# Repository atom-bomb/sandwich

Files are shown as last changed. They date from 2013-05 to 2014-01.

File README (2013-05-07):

Sandwich is a project to create low-cost electronics for 3D printing and CNC using an ATMEGA644p and TB6600 stepper drivers, not entirely unlike http://www.reprap.org/wiki/Gen7T and http://www.reprap.org/wiki/Sanguish.

The goal is to make an easily built, free and open design capable of running the Marlin firmware that can be built for around $40.

Design work is currently being done in the hobbyist-friendly Eagle CAD.
If the design exceeds the limits of the free version of Eagle CAD, the design will likely be ported to gEDA or another free CAD system in order to support the free and open design goal.

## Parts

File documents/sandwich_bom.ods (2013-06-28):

Qty | Value | Device | Package | Parts | Description | Tayda Part Number | Tayda Price / ea | Tayda Subtotal | Mouser Part Number | Mouser Price / ea | Mouser Subtotal
4 |  | JP4Q | JP4Q | JP0, JP1, JP2, JP3 | JUMPER | A-198 (http://www.taydaelectronics.com/connectors-sockets/pin-headers/2x40-pin-2-54-mm-double-row-pin-header-strip.html) | 0.28
2 |  | LED5MM | LED5MM | LED1, LED2 | LED | A-1554 (http://www.taydaelectronics.com/leds/round-leds/5mm-leds/led-5mm-red.html) | 0.02 | 0.04
3 |  | M02PTH3 | 1X02_LONGPADS | FAN, TEMP0, TEMP1 | Header 2 | A-197 (http://www.taydaelectronics.com/connectors-sockets/pin-headers/40-pin-2-54-mm-single-row-pin-header-strip.html) | 0.15
3 |  | M03LONGPADS | 1X03_LONGPADS | X_MIN, Y_MIN, Z_MIN | Header 3
1 |  | M06SIP | 1X06 | SER0 | Header 6
19 | 0.1uF | CAPPTH | CAP-PTH-SMALL | C5, C6, C7, C9, C11, C14, C15, C16, C19, C20, C21, C24, C25, C26, C27, C28, C29, C30, C31 | Capacitor | A-553 (http://www.taydaelectronics.com/capacitors/ceramic-disc-capacitors/10-x-0-1uf-50v-ceramic-disc-capacitor-pkg-of-27.html) | 0.01 | 0.19
32 | 1 | R-US_0204/2V | 0204V | R2, R3, R4, R5, R6, R7, R8, R9, R20, R21, R22, R23, R24, R25, R26, R27, R32, R33, R34, R35, R36, R37, R38, R39, R44, R45, R46, R47, R48, R49, R50, R51 | RESISTOR, American symbol | A-2031 (http://www.taydaelectronics.com/resistors/1-4w-carbon-film-resistors/10-x-resistor-1-ohm-1-4w-5-carbon-film-pkg-of-10.html) | 0.01 | 0.32
8 | 100uF | CAP_POLPTH2 | CPOL-RADIAL-10UF-25V | C3, C4, C12, C13, C17, C18, C22, C23 | Capacitor Polarized | A-4514 (http://www.taydaelectronics.com/capacitors/electrolytic-capacitors/100uf-16v-105c-radial-electrolytic-capacitor-5x11mm.html) | 0.02 | 0.16
1 | 10k | R-US_0204/2V | 0204V | R1 | RESISTOR, American symbol | A-2115 (http://www.taydaelectronics.com/resistors/1-4w-carbon-film-resistors/10-x-resistor-10k-ohm-1-4w-5-carbon-film-pkg-of-10.html) | 0.01 | 0.01
2 | 10uF | CAP_POLPTH2 | CPOL-RADIAL-10UF-25V | C8, C10 | Capacitor Polarized | A-4534 (http://www.taydaelectronics.com/capacitors/electrolytic-capacitors/10uf-25v-105c-radial-electrolytic-capacitor-5x11mm.html) | 0.02 | 0.04
2 | 1N4004 | 1N4004 | DO41-10 | D1, D2 | DIODE | A-156 (http://www.taydaelectronics.com/diodes/standard/1n4004-diode-1a-400v.html) | 0.02 | 0.04
1 | 1N4004 | DIODEPTH | DIODE-1N4001 | D3 | Diode
10 | 1k | R-US_0204/2V | 0204V | R12, R13, R14, R17, R30, R31, R42, R43, R54, R55 | RESISTOR, American symbol | A-2123 (http://www.taydaelectronics.com/resistors/1-4w-carbon-film-resistors/10-x-resistor-1k-ohm-1-4w-5-carbon-film-pkg-of-10.html) | 0.01 | 0.1
1 | 1k7 | R-US_0204/2V | 0204V | R56 | RESISTOR, American symbol | A-2084 (http://www.taydaelectronics.com/resistors/1-4w-carbon-film-resistors/10-x-resistor-1-6k-ohm-1-4w-5-carbon-film-pkg-of-10.html) | 0.01 | 0.01
1 | 20MHZ | XTAL/S | QS | Q1 | CRYSTAL | A-236 (http://www.taydaelectronics.com/crystals-resonators-oscilliators/crystals/20-000-mhz-20-mhz-crystal-hc-49-s-low-profile.html) | 0.1 | 0.1
2 | 22pF | CAPPTH2 | CAP-PTH-SMALL2 | C1, C2 | Capacitor | A-523 (http://www.taydaelectronics.com/capacitors/ceramic-disc-capacitors/10-x-22pf-50v-ceramic-disc-capacitor-pkg-of-10.html) | 0.01 | 0.02
1 | 2N2222 | 2N2222 | TO18 | T4 | NPN TRANSISTOR | A-113 (http://www.taydaelectronics.com/t-transistors/2n-series/2n2222a-2n2222-npn-transistor-0-8a-40v-to-18.html) | 0.33 | 0.33
4 | 4.7k | POTTRIM | TRIM_POT | T0, T1, T2, T3 |  | A-2511 (http://www.taydaelectronics.com/potentiometer-variable-resistors/trimmers/6mm-top-adjustment/4-7k-ohm-trimpot-variable-resistor-6mm.html) | 0.06 | 0.24
4 | 4.7k | R-US_0204/2V | 0204V | R11, R29, R41, R53 | RESISTOR, American symbol | A-2027 (http://www.taydaelectronics.com/resistors/1-4w-carbon-film-resistors/10-x-resistor-4-7k-4k7-ohm-1-4w-5-carbon-film-pkg-of-10.html) | 0.01 | 0.04
4 | 47k | R-US_0204/2V | 0204V | R10, R28, R40, R52 | RESISTOR, American symbol | A-2066 (http://www.taydaelectronics.com/resistors/1-4w-carbon-film-resistors/10-x-resistor-47k-ohm-1-4w-5-carbon-film-pkg-of-10.html) | 0.01 | 0.04
2 | 4k7 | R-US_0204/2V | 0204V | R16, R19 | RESISTOR, American symbol | A-2027 (http://www.taydaelectronics.com/resistors/1-4w-carbon-film-resistors/10-x-resistor-4-7k-4k7-ohm-1-4w-5-carbon-film-pkg-of-10.html) | 0.01 | 0.02
2 | 560 | R-US_0204/2V | 0204V | R15, R18 | RESISTOR, American symbol | A-2065 (http://www.taydaelectronics.com/resistors/1-4w-carbon-film-resistors/10-x-resistor-560-ohm-1-4w-5-carbon-film-pkg-of-10.html) | 0.01 | 0.02
1 | ATMEGA644-20PU | ATMEGA644-20PU | DIL40 | IC1 | 8-bit Microcontroller with 64K Bytes In-System Programmable Flash |  |  |  | 556-ATMEGA644PA-PU (http://www.mouser.com/ProductDetail/Atmel/ATmega644PA-PU/?qs=sGAEpiMZZMutXGli8Ay4kJfLPaXdJsZCnXM01wXS9Ts=) | 7.5 | 7.5
1 | AVR_SPI_PRG_6NS | AVR_SPI_PRG_6NS | 2X3-NS | J1 | AVR ISP 6 Pin
3 | DG3XX-02-3.5 | DG3XX-02-3.5 | DG350-3.5-02P | HEATER0, HEATER1, V+ | DG350-3.5-02P | A-4569 (http://www.taydaelectronics.com/connectors-sockets/terminal-blocks/pcb-mount/dg350-screw-terminal-block-2-positions-3-5mm.html) | 0.15 | 0.45
4 | DG3XX-04-3.5 | DG3XX-04-3.5 | DG350-3.5-04P | MOTOR0, MOTOR1, MOTOR2, MOTOR3 | DG350-3.5-04P
2 | MOSFET-NCHANNELFQP30N06L | MOSFET-NCHANNELFQP30N06L | TO220V | Q2, Q3 | Common NMOSFET Parts | A-082 (http://www.taydaelectronics.com/t-transistors/fets-mosfets/irfz44-irfz44n-mosfet-n-channel-49a-55v.html) | 0.45 | 0.9
4 | TB6600HG | TB6600HG | P-HZIP25-1.00G | U$1, U$2, U$3, U$4 |  |  |  |  | 757-TB6600HGO (http://www.mouser.com/ProductDetail/Toshiba/TB6600HGO/?qs=/ha2pyFaduir2PxFYWpWDfA69NCKMQC2ZOZZFkxtsnE=) | 7.5 | 30
 |  |  |  |  |  |  |  | 3.07 |  |  | 37.5

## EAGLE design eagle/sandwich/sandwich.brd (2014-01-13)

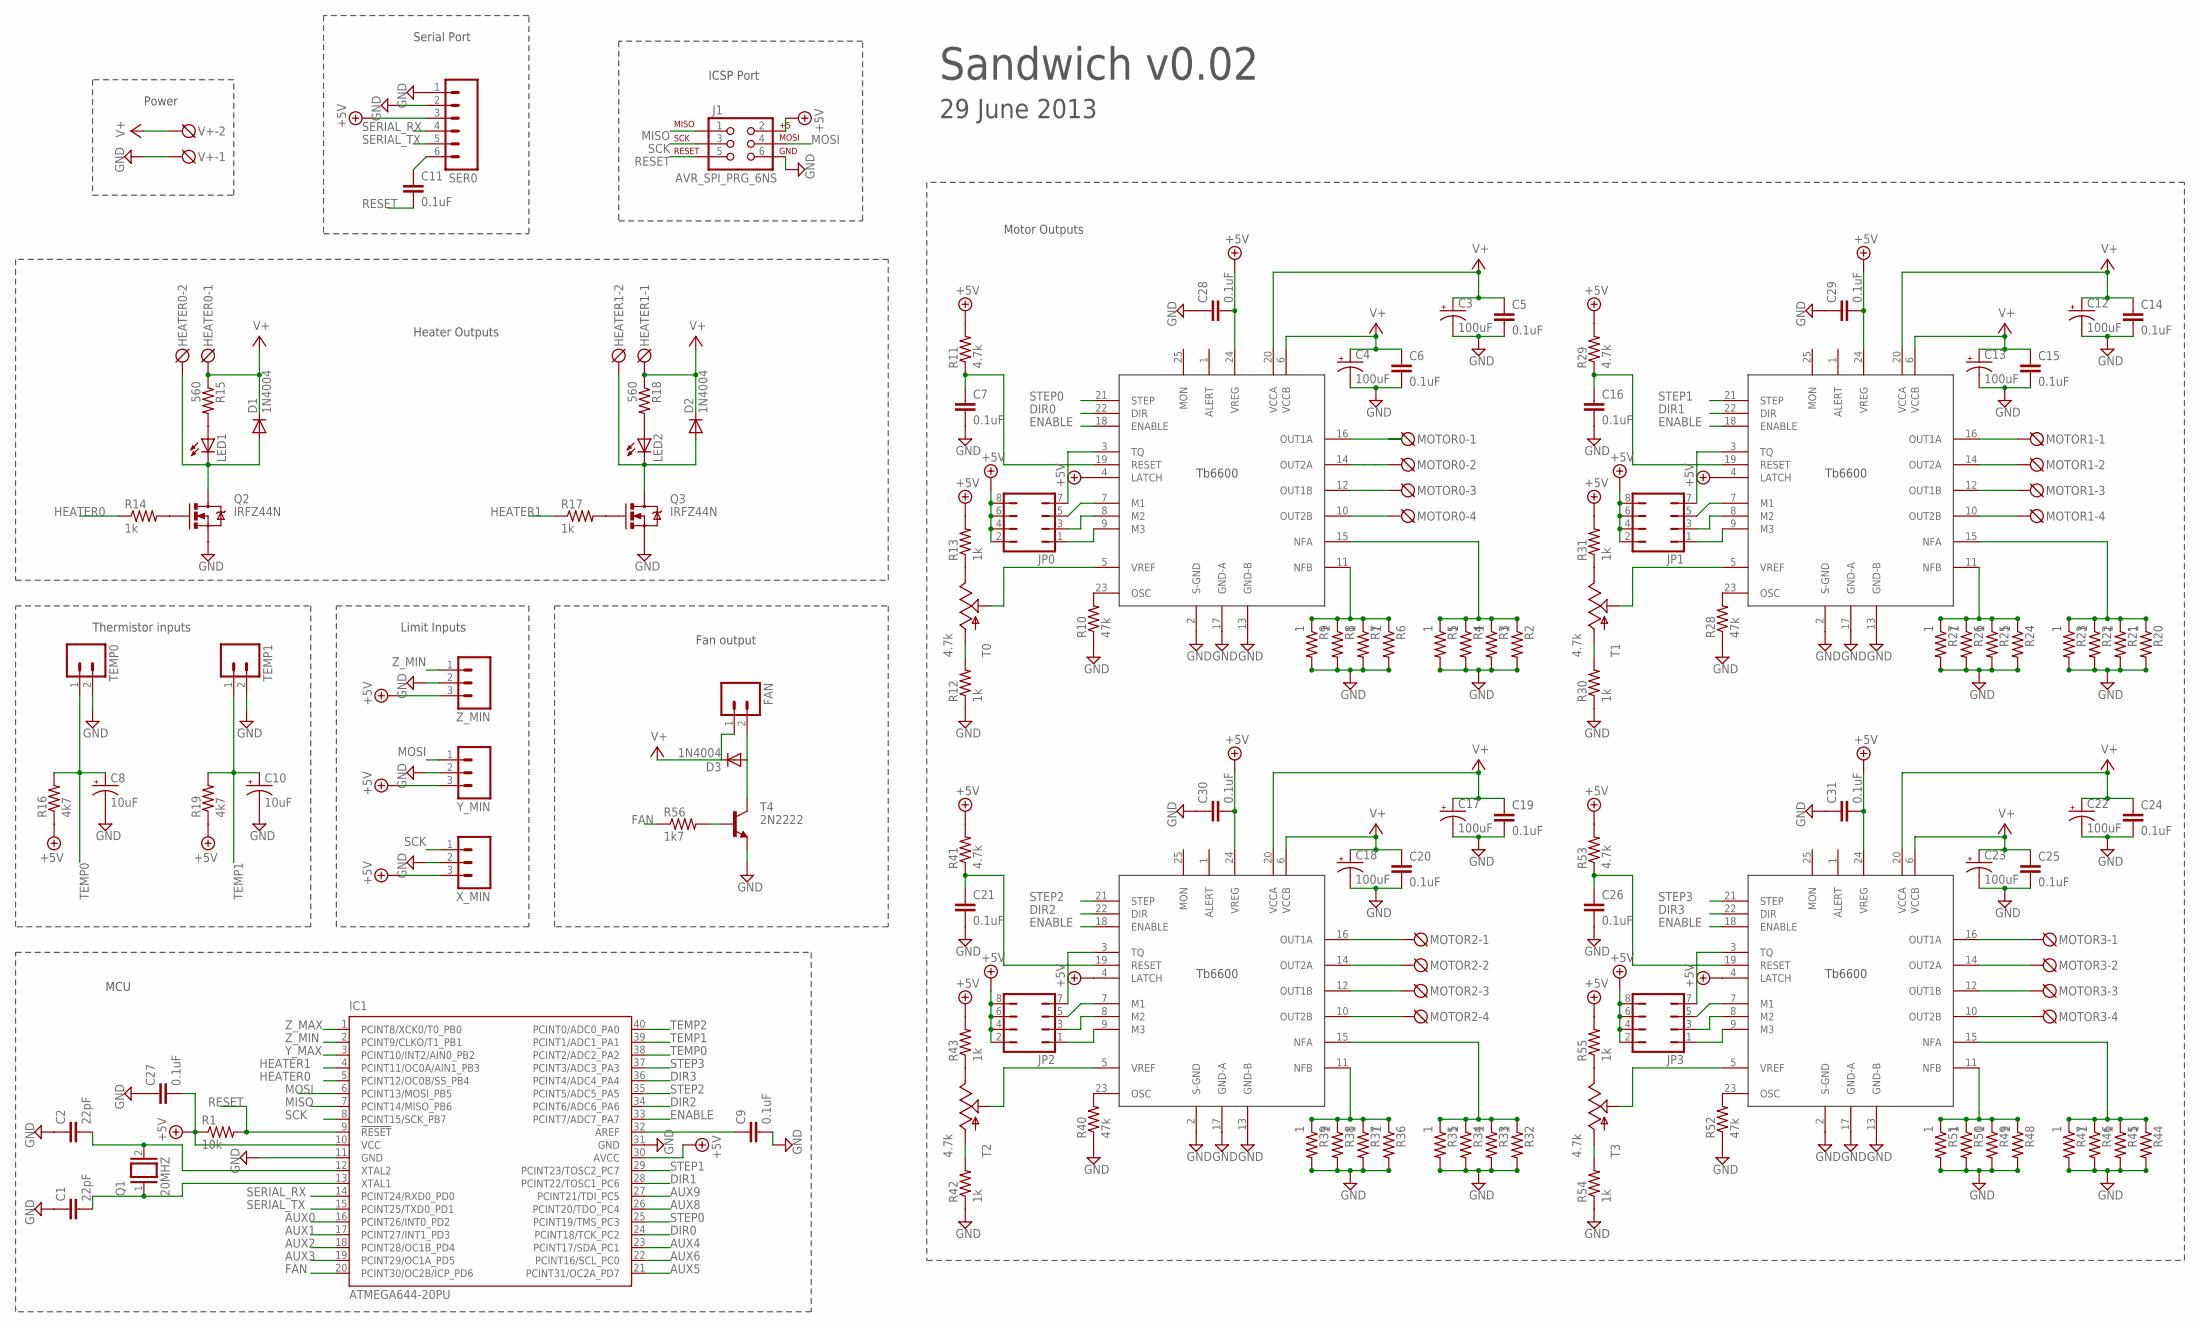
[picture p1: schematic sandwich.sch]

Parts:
C1, C2: 22pF; CAP-PTH-SMALL2
C3, C4, C12, C13, C17, C18, C22, C23: 100uF; CPOL-RADIAL-10UF-25V
C5, C6, C7, C9, C11, C14, C15, C16, C19, C20, C21, C24, C25, C26, C27, C28, C29, C30, C31: 0.1uF; CAP-PTH-SMALL
C8, C10: 10uF; CPOL-RADIAL-10UF-25V
D1, D2: 1N4004; DO41-10
D3: 1N4004; DIODE-1N4001
FAN: M02PTH3; 1X02_LONGPADS
HEATER0, HEATER1: DG3XX-02-3.5; DG350-3.5-02P
IC1: ATMEGA644-20PU; DIL40
J1: AVR_SPI_PRG_6NS; 2X3-NS
JP0, JP1, JP2, JP3: JP4Q
LED1, LED2: LED5MM
MOTOR0, MOTOR1, MOTOR2, MOTOR3: DG3XX-04-3.5; DG350-3.5-04P
Q1: 20MHZ; QS
Q2, Q3: IRFZ44N; TO220V
R1: 10k; 0204V
R2, R3, R4, R5, R6, R7, R8, R9, R20, R21, R22, R23, R24, R25, R26, R27, R32, R33, R34, R35, R36, R37, R38, R39, R44, R45, R46, R47, R48, R49, R50, R51: 1; 0204V
R10, R28, R40, R52: 47k; 0204V
R11, R29, R41, R53: 4.7k; 0204V
R12, R13, R14, R17, R30, R31, R42, R43, R54, R55: 1k; 0204V
R15, R18: 560; 0204V
R16, R19: 4k7; 0204V
R56: 1k7; 0204V
SER0: M06SIP; 1X06
T0, T1, T2, T3: 4.7k; TRIM_POT
T4: 2N2222; TO18
TEMP0, TEMP1: M02PTH3; 1X02_LONGPADS
U$1, U$2, U$3, U$4: TB6600HG; P-HZIP25-1.00G
V+: DG3XX-02-3.5; DG350-3.5-02P
X_MIN: M03LONGPADS; 1X03_LONGPADS
Y_MIN: M03LONGPADS; 1X03_LONGPADS
Z_MIN: M03LONGPADS; 1X03_LONGPADS

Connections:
+5V: C27.2, C28.2, C29.2, C30.2, C31.2, IC1.10 (VCC), IC1.30 (AVCC), J1.2, JP0.2, JP0.4, JP0.6, JP0.8, JP1.2, JP1.4, JP1.6, JP1.8, JP2.2, JP2.4, JP2.6, JP2.8, JP3.2, JP3.4, JP3.6, JP3.8, R1.1, R11.2, R13.2, R16.1, R19.1, R29.2, R31.2, R41.2, R43.2, R53.2, R55.2, SER0.3, U$1.4 (LATCH), U$1.24 (VREG), U$2.4 (LATCH), U$2.24 (VREG), U$3.4 (LATCH), U$3.24 (VREG), U$4.4 (LATCH), U$4.24 (VREG), X_MIN.3, Y_MIN.3, Z_MIN.3
AUX0: IC1.16 (PCINT26/INT0_PD2)
AUX1: IC1.17 (PCINT27/INT1_PD3)
AUX2: IC1.18 (PCINT28/OC1B_PD4)
AUX3: IC1.19 (PCINT29/OC1A_PD5)
AUX4: IC1.23 (PCINT17/SDA_PC1)
AUX5: IC1.21 (PCINT31/OC2A_PD7)
AUX6: IC1.22 (PCINT16/SCL_PC0)
AUX8: IC1.26 (PCINT20/TDO_PC4)
AUX9: IC1.27 (PCINT21/TDI_PC5)
DIR0: IC1.24 (PCINT18/TCK_PC2), U$1.22 (DIR)
DIR1: IC1.28 (PCINT22/TOSC1_PC6), U$2.22 (DIR)
DIR2: IC1.34 (PCINT6/ADC6_PA6), U$3.22 (DIR)
DIR3: IC1.36 (PCINT4/ADC4_PA4), U$4.22 (DIR)
ENABLE: IC1.33 (PCINT7/ADC7_PA7), U$1.18 (ENABLE), U$2.18 (ENABLE), U$3.18 (ENABLE), U$4.18 (ENABLE)
FAN: IC1.20 (PCINT30/OC2B/ICP_PD6), R56.1
GND: C1.1, C2.1, C3.2 (-), C4.2 (-), C5.2, C6.2, C7.2, C8.2 (-), C9.2, C10.2 (-), C12.2 (-), C13.2 (-), C14.2, C15.2, C16.2, C17.2 (-), C18.2 (-), C19.2, C20.2, C21.2, C22.2 (-), C23.2 (-), C24.2, C25.2, C26.2, C27.1, C28.1, C29.1, C30.1, C31.1, IC1.11 (GND), IC1.31 (GND), J1.6, Q2.3 (S), Q3.3 (S), R2.2, R3.2, R4.2, R5.2, R6.2, R7.2, R8.2, R9.2, R10.1, R12.1, R20.2, R21.2, R22.2, R23.2, R24.2, R25.2, R26.2, R27.2, R28.1, R30.1, R32.2, R33.2, R34.2, R35.2, R36.2, R37.2, R38.2, R39.2, R40.1, R42.1, R44.2, R45.2, R46.2, R47.2, R48.2, R49.2, R50.2, R51.2, R52.1, R54.1, SER0.1, SER0.2, T4.1 (E), TEMP0.2, TEMP1.2, U$1.2 (S-GND), U$1.13 (GND-B), U$1.17 (GND-A), U$2.2 (S-GND), U$2.13 (GND-B), U$2.17 (GND-A), U$3.2 (S-GND), U$3.13 (GND-B), U$3.17 (GND-A), U$4.2 (S-GND), U$4.13 (GND-B), U$4.17 (GND-A), V+.1, X_MIN.2, Y_MIN.2, Z_MIN.2
HEATER0: IC1.5 (PCINT12/OC0B/SS_PB4), R14.1
HEATER1: IC1.4 (PCINT11/OC0A/AIN1_PB3), R17.1
MISO: IC1.7 (PCINT14/MISO_PB6), J1.1
MOSI: IC1.6 (PCINT13/MOSI_PB5), J1.4, Y_MIN.1
unnamed: C2.2, IC1.12 (XTAL2), Q1.2
unnamed: C1.2, IC1.13 (XTAL1), Q1.1
unnamed: R10.2, U$1.23 (OSC)
unnamed: R2.1, R3.1, R4.1, R5.1, U$1.15 (NFA)
unnamed: R6.1, R7.1, R8.1, R9.1, U$1.11 (NFB)
unnamed: MOTOR0.4, U$1.10 (OUT2B)
unnamed: MOTOR0.3, U$1.12 (OUT1B)
unnamed: MOTOR0.2, U$1.14 (OUT2A)
unnamed: MOTOR0.1, U$1.16 (OUT1A)
unnamed: R12.2, T0.3 (A)
unnamed: R13.1, T0.2 (E)
unnamed: T0.1 (S), U$1.5 (VREF)
unnamed: Q2.1 (G), R14.2
unnamed: LED1.A, R15.2
unnamed: D1.A, HEATER0.2, LED1.K (C), Q2.2 (D)
unnamed: C7.1, R11.1, U$1.19 (RESET)
unnamed: C9.1, IC1.32 (AREF)
unnamed: JP0.1, U$1.9 (M3)
unnamed: Q3.1 (G), R17.2
unnamed: LED2.A, R18.2
unnamed: D2.A, HEATER1.2, LED2.K (C), Q3.2 (D)
unnamed: JP0.3, U$1.8 (M2)
unnamed: JP0.5, U$1.7 (M1)
unnamed: JP0.7, U$1.3 (TQ)
unnamed: C11.1, SER0.6
unnamed: D3.A, FAN.2, T4.3 (C)
unnamed: R20.1, R21.1, R22.1, R23.1, U$2.15 (NFA)
unnamed: R24.1, R25.1, R26.1, R27.1, U$2.11 (NFB)
unnamed: R28.2, U$2.23 (OSC)
unnamed: MOTOR1.1, U$2.16 (OUT1A)
unnamed: MOTOR1.2, U$2.14 (OUT2A)
unnamed: MOTOR1.3, U$2.12 (OUT1B)
unnamed: MOTOR1.4, U$2.10 (OUT2B)
unnamed: C16.1, R29.1, U$2.19 (RESET)
unnamed: R30.2, T1.3 (A)
unnamed: R31.1, T1.2 (E)
unnamed: T1.1 (S), U$2.5 (VREF)
unnamed: JP1.1, U$2.9 (M3)
unnamed: JP1.3, U$2.8 (M2)
unnamed: JP1.5, U$2.7 (M1)
unnamed: JP1.7, U$2.3 (TQ)
unnamed: R32.1, R33.1, R34.1, R35.1, U$3.15 (NFA)
unnamed: R36.1, R37.1, R38.1, R39.1, U$3.11 (NFB)
unnamed: R40.2, U$3.23 (OSC)
unnamed: MOTOR2.1, U$3.16 (OUT1A)
unnamed: MOTOR2.2, U$3.14 (OUT2A)
unnamed: MOTOR2.3, U$3.12 (OUT1B)
unnamed: MOTOR2.4, U$3.10 (OUT2B)
unnamed: C21.1, R41.1, U$3.19 (RESET)
unnamed: R42.2, T2.3 (A)
unnamed: R43.1, T2.2 (E)
unnamed: T2.1 (S), U$3.5 (VREF)
unnamed: JP2.1, U$3.9 (M3)
unnamed: JP2.3, U$3.8 (M2)
unnamed: JP2.5, U$3.7 (M1)
unnamed: JP2.7, U$3.3 (TQ)
unnamed: R44.1, R45.1, R46.1, R47.1, U$4.15 (NFA)
unnamed: R48.1, R49.1, R50.1, R51.1, U$4.11 (NFB)
unnamed: R52.2, U$4.23 (OSC)
unnamed: MOTOR3.1, U$4.16 (OUT1A)
unnamed: MOTOR3.2, U$4.14 (OUT2A)
unnamed: MOTOR3.3, U$4.12 (OUT1B)
unnamed: MOTOR3.4, U$4.10 (OUT2B)
unnamed: C26.1, R53.1, U$4.19 (RESET)
unnamed: R54.2, T3.3 (A)
unnamed: R55.1, T3.2 (E)
unnamed: T3.1 (S), U$4.5 (VREF)
unnamed: JP3.1, U$4.9 (M3)
unnamed: JP3.3, U$4.8 (M2)
unnamed: JP3.5, U$4.7 (M1)
unnamed: JP3.7, U$4.3 (TQ)
unnamed: R56.2, T4.2 (B)
RESET: C11.2, IC1.9 (!RESET), J1.5, R1.2
SCK: IC1.8 (PCINT15/SCK_PB7), J1.3, X_MIN.1
SERIAL_RX: IC1.14 (PCINT24/RXD0_PD0), SER0.4
SERIAL_TX: IC1.15 (PCINT25/TXD0_PD1), SER0.5
STEP0: IC1.25 (PCINT19/TMS_PC3), U$1.21 (STEP)
STEP1: IC1.29 (PCINT23/TOSC2_PC7), U$2.21 (STEP)
STEP2: IC1.35 (PCINT5/ADC5_PA5), U$3.21 (STEP)
STEP3: IC1.37 (PCINT3/ADC3_PA3), U$4.21 (STEP)
TEMP0: C8.1 (+), IC1.38 (PCINT2/ADC2_PA2), R16.2, TEMP0.1
TEMP1: C10.1 (+), IC1.39 (PCINT1/ADC1_PA1), R19.2, TEMP1.1
TEMP2: IC1.40 (PCINT0/ADC0_PA0)
V+: C3.1 (+), C4.1 (+), C5.1, C6.1, C12.1 (+), C13.1 (+), C14.1, C15.1, C17.1 (+), C18.1 (+), C19.1, C20.1, C22.1 (+), C23.1 (+), C24.1, C25.1, D1.C, D2.C, D3.C, FAN.1, HEATER0.1, HEATER1.1, R15.1, R18.1, U$1.6 (VCCB), U$1.20 (VCCA), U$2.6 (VCCB), U$2.20 (VCCA), U$3.6 (VCCB), U$3.20 (VCCA), U$4.6 (VCCB), U$4.20 (VCCA), V+.2
Y_MAX: IC1.3 (PCINT10/INT2/AIN0_PB2)
Z_MAX: IC1.1 (PCINT8/XCK0/T0_PB0)
Z_MIN: IC1.2 (PCINT9/CLKO/T1_PB1), Z_MIN.1

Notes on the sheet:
Thermistor inputs
Limit Inputs
Heater Outputs
Serial Port
ICSP Port
Power
Motor Outputs
MCU
Sandwich v0.02
29 June 2013
Fan output

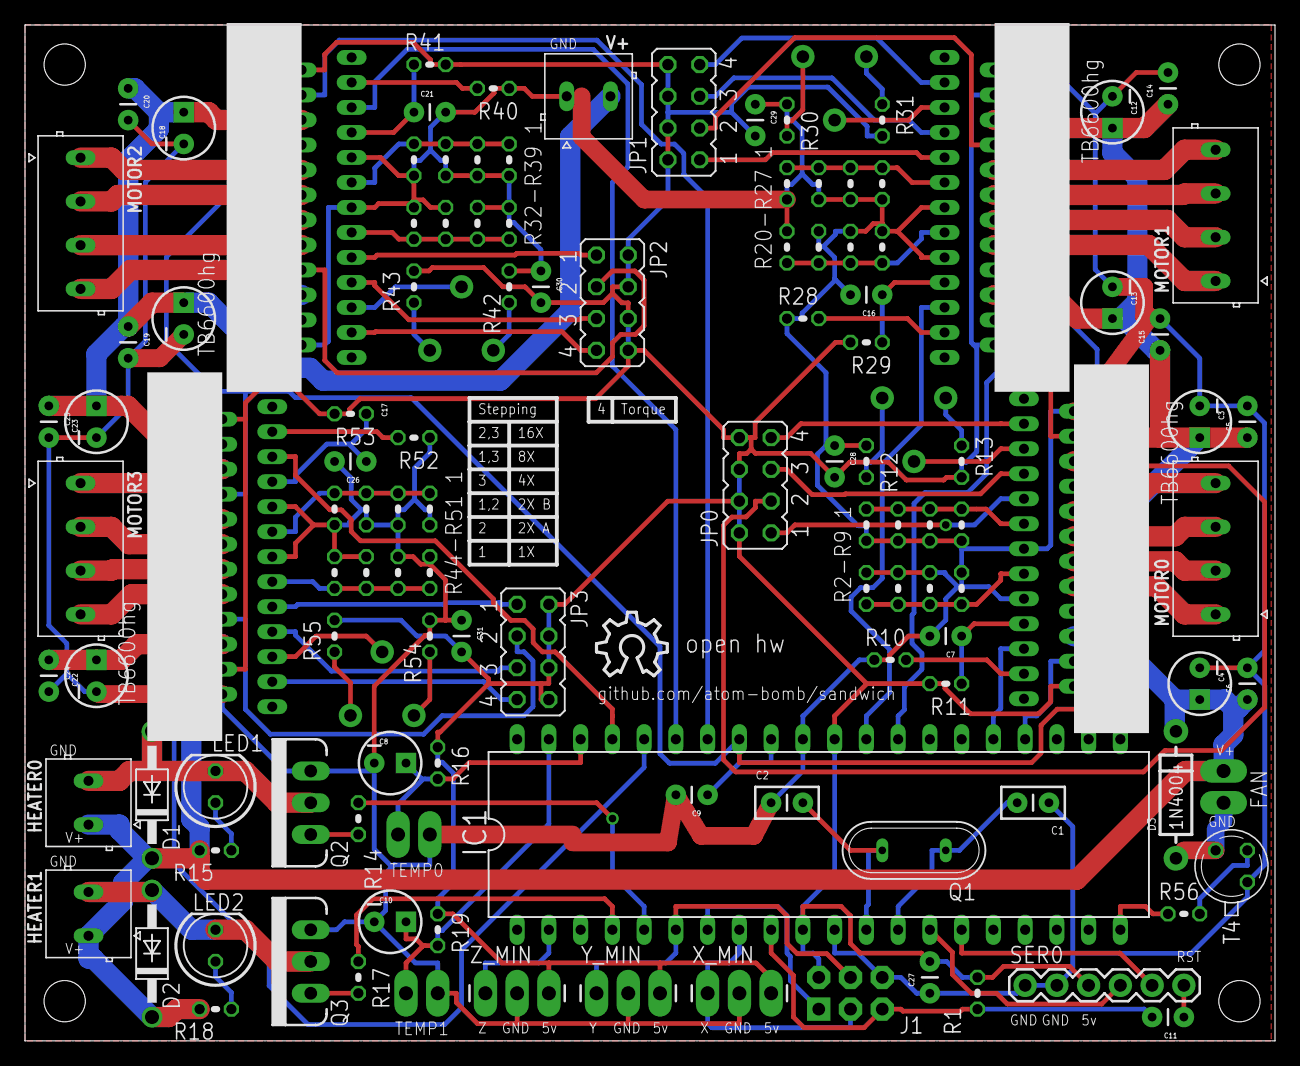
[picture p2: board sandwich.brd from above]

Board: 2 copper layers, 100.0 x 81.3 mm, 129 parts (0 on the bottom side), 96 nets.

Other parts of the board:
U$5, U$6, U$7, U$8: STAND-OFF
U$9: OSHW_10X200_NOTEXT

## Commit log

2013-05-07 First commit of Sandwich, including a schematic!
    [sandwich.sch]
2013-05-07 issue#5: added decoupling caps
    [sandwich.sch]
2013-05-08 Changed all screw terminals to the smaller DG350
    [sandwich.sch]
2013-05-08 reorganized for 11x17 printability, added title and date text
    [sandwich.sch]
2013-05-09 AVR pin assignments are now the same as Gen7t. Motor enables are now combined.
    [sandwich.sch]
2013-05-09 Changed all connectors except V+ and heaters to pin headers, removed axis max inputs
    [sandwich.sch]
2013-05-11 The beginnings of a board layout
    [sandwich.brd]
2013-05-15 Changed motor connectors back to screw terminals, added a fan output and routed the board layout.
    [sandwich.brd, sandwich.sch]
2013-05-15 Changed trim pots to 4.7k
    [sandwich.brd, sandwich.sch]
2013-06-01 This seems like a millable layout and routing
    [sandwich.brd, sandwich.sch]
2013-06-25 Updated TB6600 package, moved R56, changed 100uF caps to 16v, disabled GND and V+ thermals. Still needs TB6600HG layout adjustment and new routing
    [sandwich.brd, sandwich.sch]
2013-06-28 A grid with some parts, suppliers and prices
    [sandwich_bom.ods]
2013-06-29 Moved FAN to a PWM output
    [sandwich.sch]
2013-06-30 Adjusted layout for larger TB6600 package, routed with improved traces for V+ and GND
    [sandwich.brd]
2013-07-01 Cleaned up the silkscreen layer
    [sandwich.brd]
2013-07-03 beefed up some traces
    [sandwich.brd]
2013-10-15 added AMT and Open HW logos
    [sandwich.brd]
2013-12-04 Fatten up a few ground traces...just in case.
    [sandwich.brd]
2013-12-05 eagle 6.5 + oshpark DRU compliance
    [sandwich.brd]
2014-01-09 labeled GND, 5v and V+ on polarized connections
    [sandwich.brd]
2014-01-12 Added documentation for jumper settings
    [sandwich.brd]
2014-01-13 AMT logo is now oshpark-friendly
    [sandwich.brd]

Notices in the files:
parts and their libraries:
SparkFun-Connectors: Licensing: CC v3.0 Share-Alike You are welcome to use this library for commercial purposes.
